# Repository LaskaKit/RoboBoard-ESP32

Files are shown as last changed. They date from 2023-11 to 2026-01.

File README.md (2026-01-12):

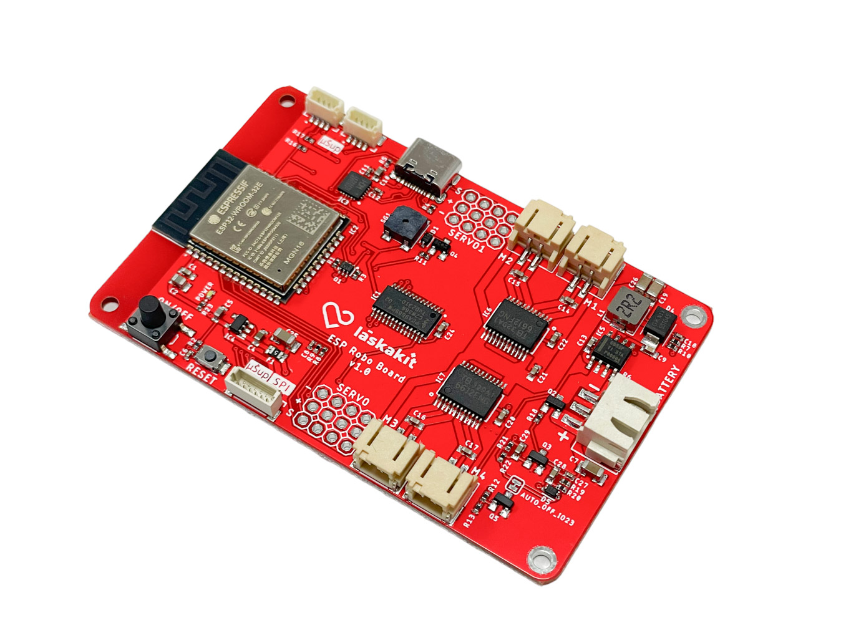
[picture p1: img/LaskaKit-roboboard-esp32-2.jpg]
RoboBoard-ESP32


# LaskaKit RoboBoard ESP32
Build a robot! Don't worry, it's nothing complicated. It's easy with our RoboBoard-ESP32. The RoboBoard has everything you need for a simple robot on it, and you can make it into a much more complex robot over time thanks to the expansion connectors for both the I2C and SPI bus. 

You can connect a lot of other peripherals. 

The basis of the whole board is ESP32 - it hides a great performance, the possibility to use Wi-Fi or Bluetooth interface and also a large community of DIY makers who have already invented many projects with it. It is not something unknown - ESP32 is one of the most well-known and used modules ever. 

The RoboBoard-ESP32 has a ready-to-use programmer (CH9102F), just plug the USB-C cable into the board and your computer, start the Arduino IDE and you can start programming. The converter-programmer will take care of uploading the program to the ESP32. 

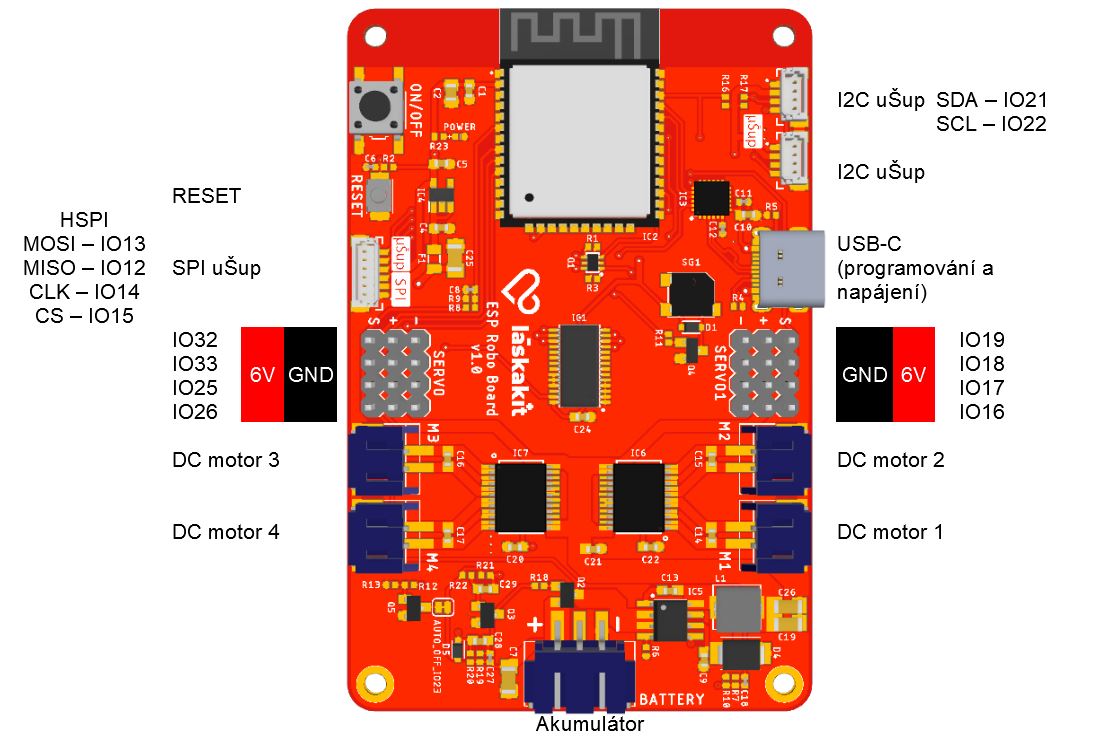
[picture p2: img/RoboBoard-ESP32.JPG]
RoboBoard-ESP32 pinout


The RoboBoard-ESP32 can drive up to 4 DC motors using PWM, thanks to the TB6612 driver. The maximum continuous current through one channel is 1A. The TB6612 DC motor driver is controlled via the PCA9685, which is controlled via the I2C bus. So you only need two wires (I2C, SDA - GPIO21 and SCL - GPIO22) to drive up to 4 DC motors. 

If you don't want to use DC motors or on the contrary you would like to add Servos to them, RoboBoard-ESP32 is ready for this option as well. 
You can connect up to 8 servo motors - what you use the servo motors for is up to you. The individual servo motors are controlled by GPIO16 to GPIO19, then GPIO25 and GPIO26 and lastly GPIO32 and GPIO33. 

What else have we prepared on the board? We have fitted a buzzer, you can control it via GPIO27. Then we have fitted two I2C ushup connectors to connect I2C sensors that are powered by 3.3V (SDA - GPIO21 and SCL - GPIO22) and one SPI ushup to connect other sensors or displays powered by 3.3V (CS - GPIO15, SDI/MOSI - GPIO13, CLK - GPIO14, SDO/MISO - GPIO12).

For the battery, we have a standard 3-pin JST-XH-3P connector where you plug in 2S LiPol batteries - for example this one https://www.laskakit.cz/rc-lipol-baterie-2s-1000mah-7-4v-20c-jst-bec/

The motors are powered via the LMR14050 step-down switching inverter from the 2S battery, which can deliver up to 5A. 

The battery voltage, via the voltage divider, is fed and measured by GPIO34. 

## New in version 2
- Powering via USB
- LiPol charging via USB
- uŠup IO port
- SK6812 RGB LED
- Overall more robust design

Sample codes will be prepared on our github at https://github.com/LaskaKit/RoboBoard-ESP32/tree/main/SW

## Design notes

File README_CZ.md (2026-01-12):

RoboBoard-ESP32

# LaskaKit RoboBoard ESP32 v2

Postav robota! Neboj, není to nic složitého. S naší deskou RoboBoard-ESP32 to bude hračka. RoboBoard totiž má na sobě všechno důležité pro jednoduchého robota a časem z něj můžeš udělat i mnohem komplexnějšího robota díky rozšiřujícím konektorům pro IO a navíc I2C a SPI sběrnice. 

Připojit tak můžeš bezpočet dalších periférií. 

Základem celé desky je ESP32 - ten v sobě skrývá velký výkon, možnost využít Wi-Fi nebo Bluetooth rozhraní a také velkou komunitu bastlířů, kteří s ním vymysleli už spoustu projektů. Nejdeš do neznámé vody - ESP32 je jeden z nejznámějších a nejpoužívanějších modulů vůbec. 

RoboBoard-ESP32 má na sobě už připravený programátor (CH9102F), stačí zapojit USB-C kabel do desky a tvého počítače, spustit Arduino IDE a můžeš začít programovat. Převodník-programátor se postará o nahrání programu do ESP32. 

RoboBoard-ESP32 pinout

RoboBoard-ESP32 může řídt až 4 DC motory pomocí PWM, díky driveru TB6612. Maximální trvalý proud skrze jeden kanál je 1A. Driver DC motorů TB6612 je řízen přes PCA9685, který je ovládán skrze I2C sběrnici. Takže ti stačí dva dráty (I2C, SDA - GPIO21 a SCL - GPIO22) k tomu, abys řídil až 4 DC motory. 

Pokud nechceš používat DC motory nebo naopak bys k nim chtěl přidat Serva, RoboBoard-ESP32 je připraven i na tuto možnost. 
Až 8 servo motorů můžeš připojit - k čemu servo motory použiješ už je jenom na tobě. Jednotlivé servo motory řídíš GPIO16 až GPIO19, dále pak GPIO25 a GPIO26 a poslední GPIO32 a GPIO33. 

Co dalšího jsme na desce ještě připravili? Osadili jsme bzučák, ten můžeš ovládat skrze GPIO27. Pak jsme osadili dva I2C uŠup konektor pro připojení I2C čidel, které jsou napájeny 3.3V (SDA - GPIO21 a SCL - GPIO22) a jeden SPI uŠup pro připojení dalších čidel či displejů napájených z 3.3V (CS - GPIO15, SDI/MOSI - GPIO13, CLK - GPIO14, SDO/MISO - GPIO12).

Pro baterii máme připraven standardní tří pinový konektor JST-XH-3P, kam zapojíš 2S LiPol baterie - například tuto https://www.laskakit.cz/rc-lipol-baterie-2s-1000mah-7-4v-20c-jst-bec/

Motory jsou napájené přes spínací step-down měnič LMR14050 z 2S baterie, který dokáže dodat až 5A. 

Napětí baterie, přes dělič napětí, je přivedeno a měřeno GPIO34. 

## Nově ve verzi 2
- Napájení přes USB
- Nabíjení LiPol baterie
- uŠup IO
- SK6812 RGB dioda
- Výrazně vyšší robustnost

Vzorové kódy budou připraveny na našem github na adrese https://github.com/LaskaKit/RoboBoard-ESP32/tree/main/SW

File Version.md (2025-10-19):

#### Version 2.0
- All new version.
- 2S Battery charger
#### Version 1.0
- Initial | Počáteční

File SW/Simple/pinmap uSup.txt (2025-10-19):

SPI uŠup
---------

MISO    12
MOSI    13
SCK     14
CS      15

I2C uŠup
--------

SDA     21
SCL     22

IO uŠup
--------

IO      5

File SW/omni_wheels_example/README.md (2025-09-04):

# Laska Omni Car Example

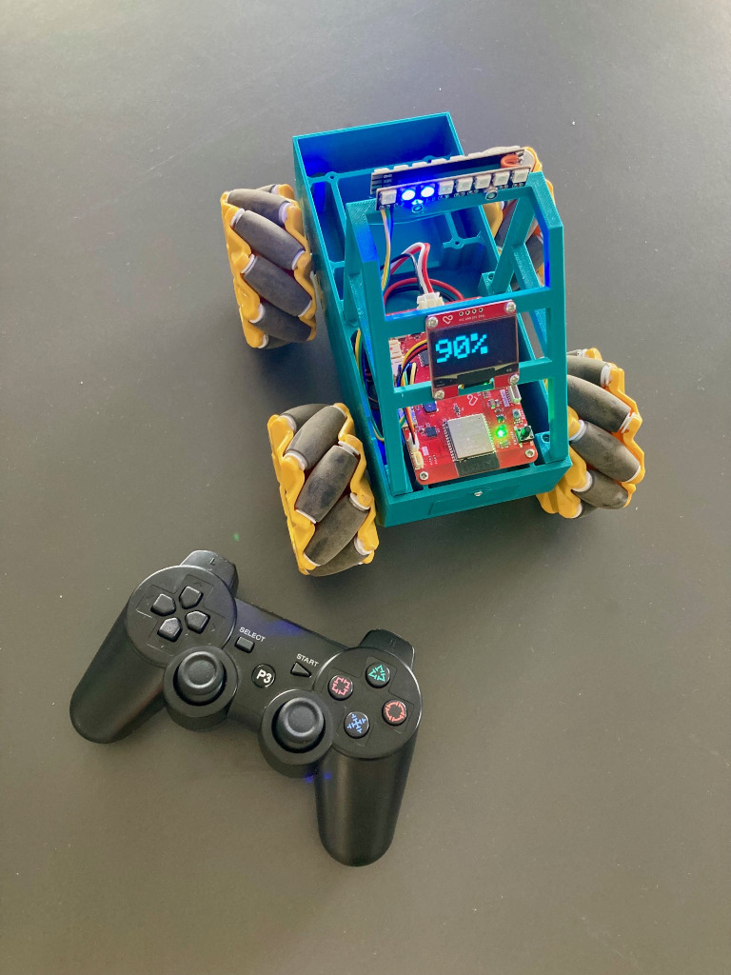
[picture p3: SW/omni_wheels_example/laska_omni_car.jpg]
Laska OmniCar


This example consists of 2 parts.

1. The vehicle with omni wheels.
2. The gamepad for vehicle control.

The vehicle and gamepad are communicating via ESP-NOW protocol.

## How to setup

1. Optain MAC addresses of gamepad and the roboboard using the sketch in `get_mac_address` directory.
2. Set the MAC address of the gamepad in the `fw_laska_omni_car` sketch and flash the roboboard.
3. Set the MAC address of the roboboard in the `fw_laska_omni_gamepad` sketch and flash the gamepad.
4. Enjoy!

### Optionally

You can setup your own LMK and PMK keys to keep the communication between roboboard and gamepad secure.
Note that keys on roboboard must be identical to those on gamepad.

## Controls

| *Input* | *Description* |
| --- | --- |
| left stick (left/right) | left/right spin |
| right stick (up/down) | forward/backward motion |
| right stick (left/right) | left/right motion |
| L1 | headlights |
| triangle | starts the beacon |
| square | stops the beacon |
| cross | horn |
| P3 (1.5s hold) | power off |

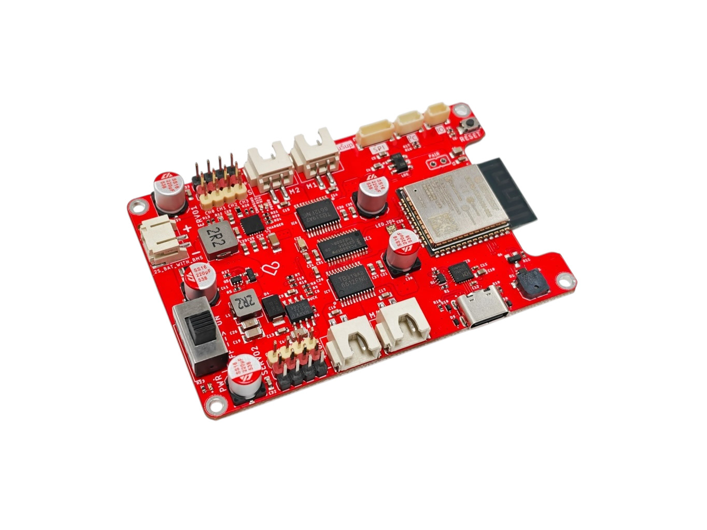
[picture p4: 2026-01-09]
img/LaskaKit-roboboard-esp32-v2-3.jpg

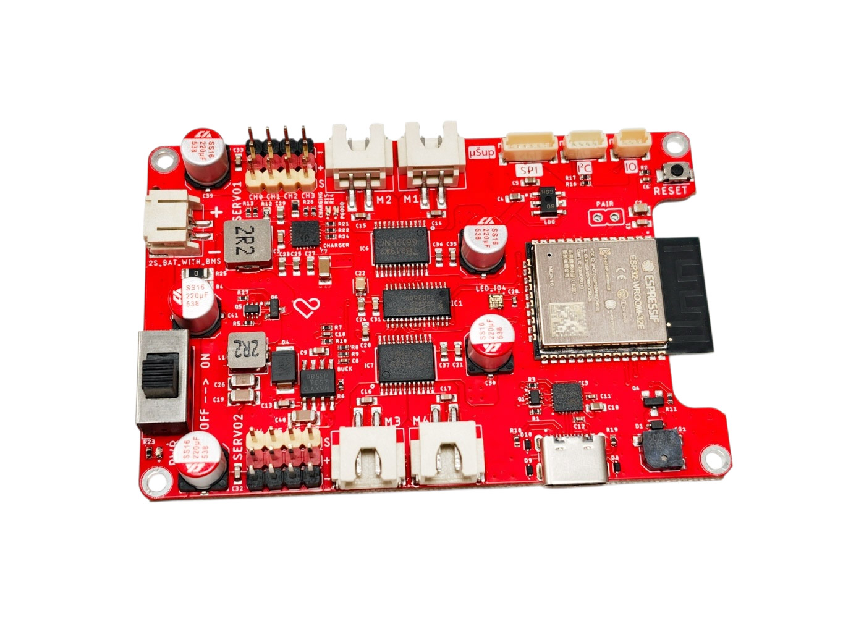
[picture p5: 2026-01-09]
img/LaskaKit-roboboard-esp32-v2-2.jpg

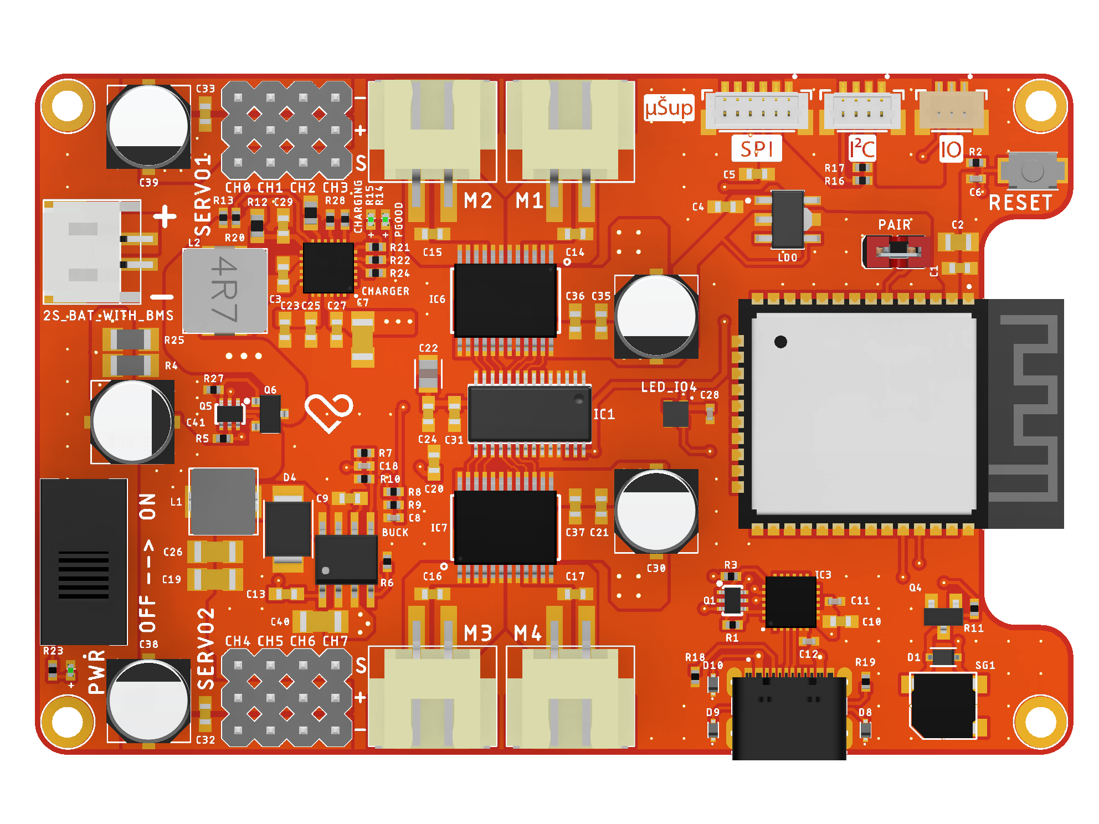
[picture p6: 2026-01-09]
img/roboboard-esp32-v2_top_render.png

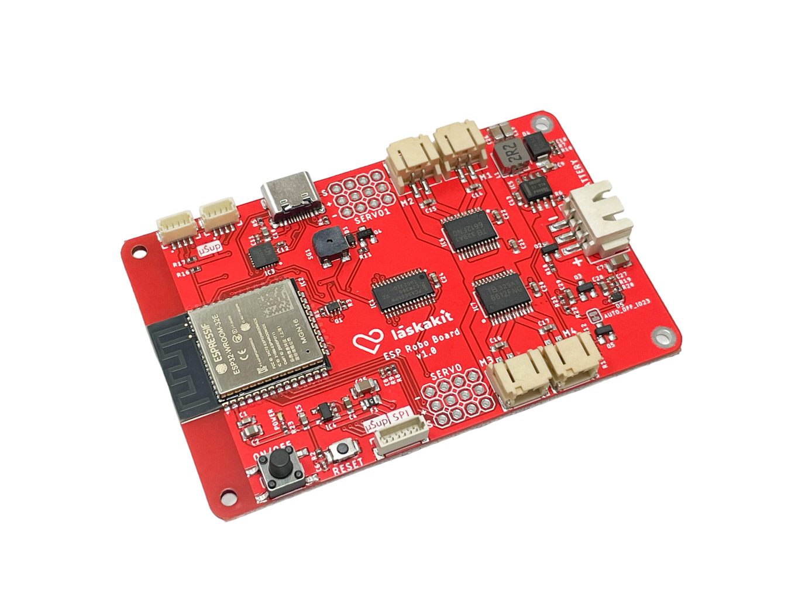
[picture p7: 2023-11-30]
img/V1/LaskaKit-roboboard-esp32-1.jpg

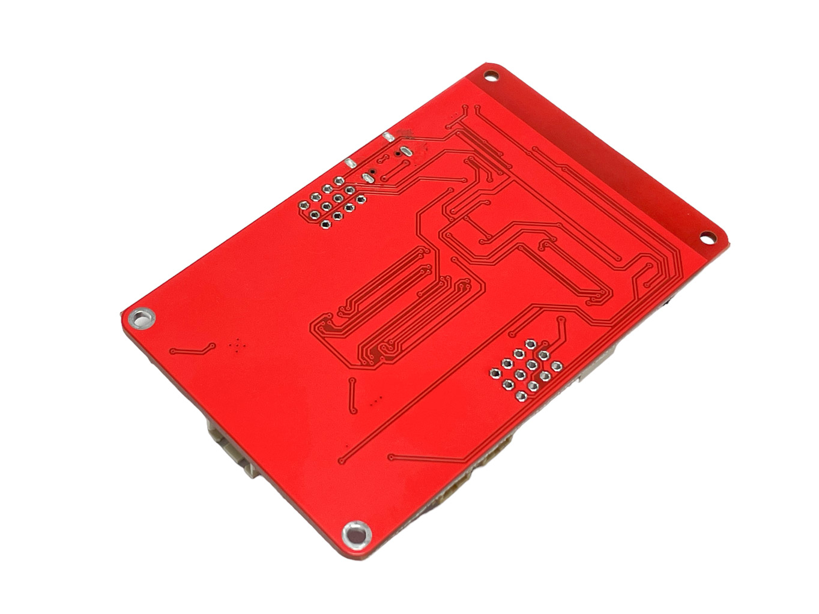
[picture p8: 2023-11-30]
img/V1/LaskaKit-roboboard-esp32-3.jpg

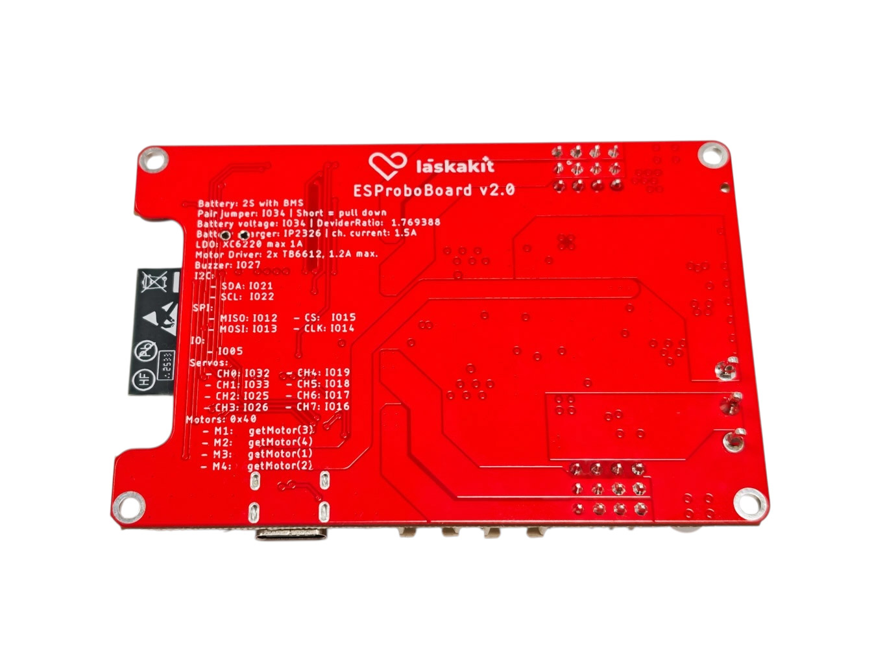
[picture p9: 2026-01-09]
img/LaskaKit-roboboard-esp32-v2-5.jpg

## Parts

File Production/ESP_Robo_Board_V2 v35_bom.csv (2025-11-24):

Comment | Designator | Footprint | LCSC Part #
0.5R | R12 | R0603
0R | R4 R25 | R1206
1N4148 | D1 | SOD323-R | C94001
1k | R11 R14 R15 R21 R22 | R0402
2.2uH | L1 | L5.4X5.2 | C351096
2.2uH | L2 | L6.6X7 | C167218
2S bat with BMS | 2S_BAT_WITH_BMS | S2B-PH-SM4 | C47647
3.3k | R23 | R0402
4.7k | R16 R17 | R0402
4.7uF | C24 | C0603
5.1k | R13 R18 R19 | R0402
8.2nF | C9 | C0603
10k | R1 R2 R3 | R0402
10uF | C23 C25 C27 C29 C36 C37 | C0603
10uF/10V | C5 | C0603 | C19666
10uF/16 | C4 | C0603
13k | R10 | R0402
20k | R6 | R0402
22uF | C10 | C0603
47k | R5 R27 | R0402
47uF | C2 | C0805
51k | R20 R24 | R0402
59.7k | R28 | R0603
91k | R7 | R0402
100k | R8 | R0402
100nF | C1 C3 | C0603
100nF | C6 C8 C11 C12 | C0402
100nF | C13 C14 C15 C16 C17 C20 C21 | C0603
100nF | C28 | C0402
100nF | C31 C32 C33 C35 | C0603
100uF | C7 C19 | C1206
100uF | C22 | C0805 | C141660
100uF | C26 C40 | C1206
130k | R9 | R0402
220uF/16V 5-20m? | C30 C34 C38 C39 C41 | UD-6 3X7 7_NICHICON | C3035876
330pF | C18 | C0402
CH9102F | IC3 | QFN24-4X4
DMG2305UX | Q6 | MICRO3 | C144153
ESP32-WROOM-32E | IC2 | ESP32WROOM32E | C701343
FUET-5020 | SG1 | FUET-5020 | C391029
GREEN | DONE POWER | CHIPLED_0402 | C130722
IP2326 | CHARGER | QFN24-4X4 | C5441281
JST-SH-3P | J4 | 1X03_1MM_RA_VERT | C160389
JST-SH-4P | J3 | 1X04_1MM_RA_VERT | C371588
JST-SH-6P | J1 | 1X06_1MM_RA_VERT | C145963
JST-XH-2/90SMD | M1 M2 M3 M4 | S2B-XH-SM4
LESD5D5.0CT1G | D8 D9 D10 | LESD5D50CT1G
LMR14050DDAR | BUCK | SO08-EPAD | C155484
MMDT3904 | Q1 | SC70-6 | C268586
MMDT5401 | Q5 | SC70-6 | C54540
PCA9685PW 118 | IC1 | TSSOP28 | C2678753
RED | CHARGING | CHIPLED_0402
S9013 | Q4 | SOT23-BEC | C52801
SK6812-EC20 | LED_IO4 | SK6812EC20
SS1045-SMB | D4 | SMB | C2903947
TB6612FNG | IC6 IC7 | SSOP24
TS-1088R-02026 | RESET | TS1088R02026 | C455280
USB-C_GT-USB-7010B | J2 | G-SWITCH_GT-USB-7010B | C2837092
XC6220B331PR-G | LDO | XC6220B331PRG
SS-12D10L5 | S1 | SS-12D10L5 | C319012
PINHD_1X4_BLACK | 2 6 | PINHD_1X4_BLACK | C2691448
PINHD_1X4_RED | 1 5 | PINHD_1X4_RED | C41425294
PINHD_1X4_YELLOW | SERVO1 SERVO2 | PINHD_1X4_YELLOW | C41425307

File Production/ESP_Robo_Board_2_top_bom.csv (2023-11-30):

Comment | Designator | Footprint | LCSC Part #
1M | R8 | R0402
1N4148 | D1 D5 | SOD323-R
1k | R11 R23 | R0402
1uF | C28 C29 | C0603
2.2uH | L1 | L5.4X5.2 | C351096
4.7k | R16 R17 | R0402
5.1k | R4 R5 | R0402
8.2n | C9 | C0603
10k | R1 R2 R3 R12 R20 | R0402
13k | R10 | R0402
20k | R6 | R0402
22uF | C4 C5 C10 | C0603
47uF | C2 | C0805
91k | R7 | R0402
100k | R13 R18 R19 R21 | R0402
100n | C11 C12 | C0402
100n | C13 C14 C15 C16 C17 C20 C21 C22 C24 | C0603
100nF | C1 | C0603
100nF | C6 C8 C27 | C0402
100uF | C7 C19 C25 C26 | C1206
330p | C18 | C0402
620k | R9 R22 | R0402
0805L050 | F1 | 0805L | C66452
AO3400 | Q3 Q5 | SOT23 | C693097
CH9102F | IC3 | QFN24-4X4
ESP32-WROOM-32E | IC2 | ESP32WROOM32E
FUET-5020 | SG1 | FUET-5020 | C391029
GREEN | POWER | CHIPLED_0402
JST-PH-2/90SMD | M1 M2 M3 M4 | S2B-PH-SM4 | C47647
JST-SH-4P | J3 J5 | 1X04_1MM_RA_VERT | C371588
JST-SH-6P | J1 | 1X06_1MM_RA_VERT | C145963
JST-XH-3P/90SMD | BATTERY | S3B-XH-SM4
LMR14050DDAR | IC5 | SO08-EPAD | C155484
ME6211C33M5G | IC4 | SOT23-5
MMDT3904 | Q1 | SC70-6 | C268586
PCA9685PW 118 | IC1 | TSSOP28 | C2678753
PJM07P20SA | Q2 | SOT23 | C2856842
S9013 | Q4 | SOT23-BEC | C52801
SS1045-SMB | D4 | SMB | C2903947
TB6612FNG | IC6 IC7 | SSOP24
TS-1088R-02026 | RESET | TS1088R02026 | C455280
TS-1102S-B-H-B | ON/OFF | B3F-SMD
USB-C_2-16PIN | J4 | USBC_USB-C-16P-5 | C2837092

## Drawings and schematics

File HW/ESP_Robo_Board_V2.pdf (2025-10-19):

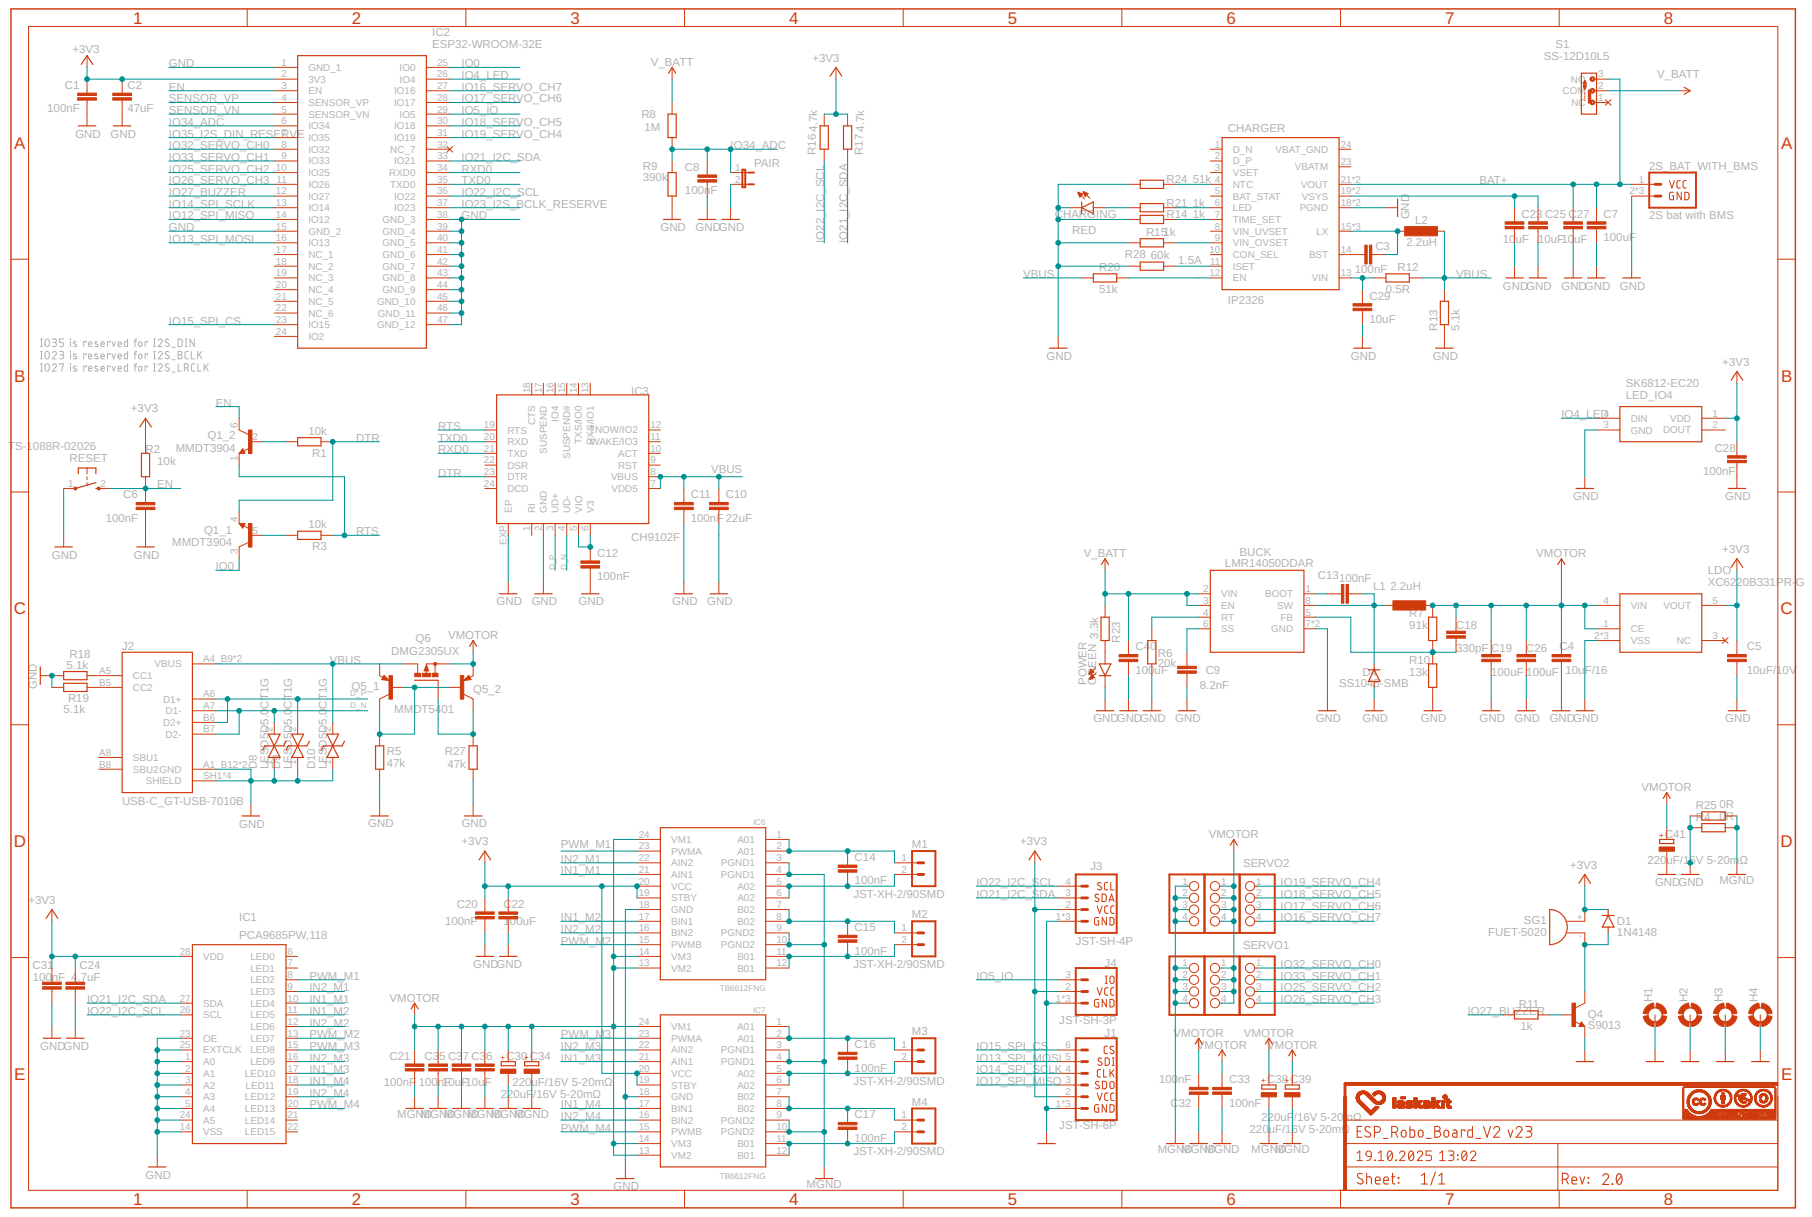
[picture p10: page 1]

IC2 GND_1

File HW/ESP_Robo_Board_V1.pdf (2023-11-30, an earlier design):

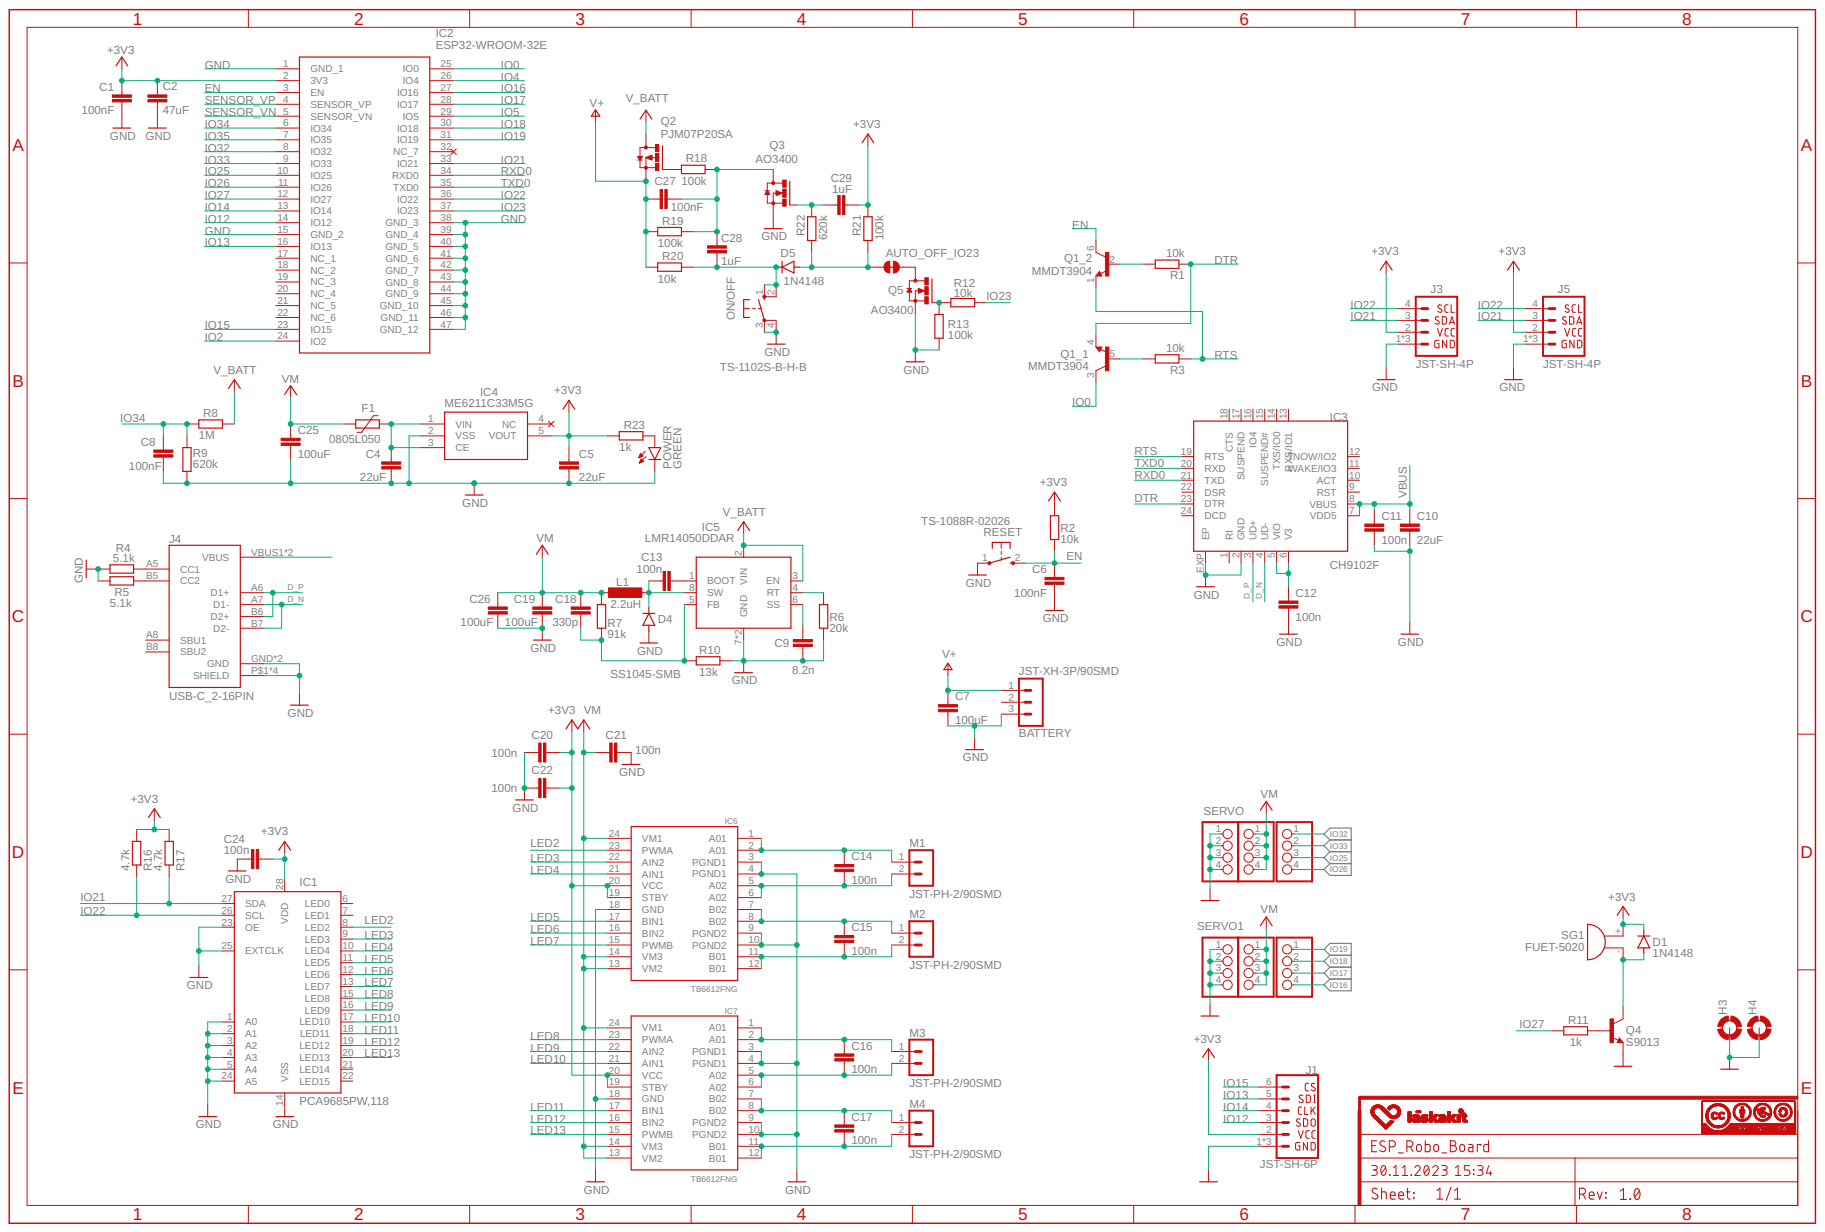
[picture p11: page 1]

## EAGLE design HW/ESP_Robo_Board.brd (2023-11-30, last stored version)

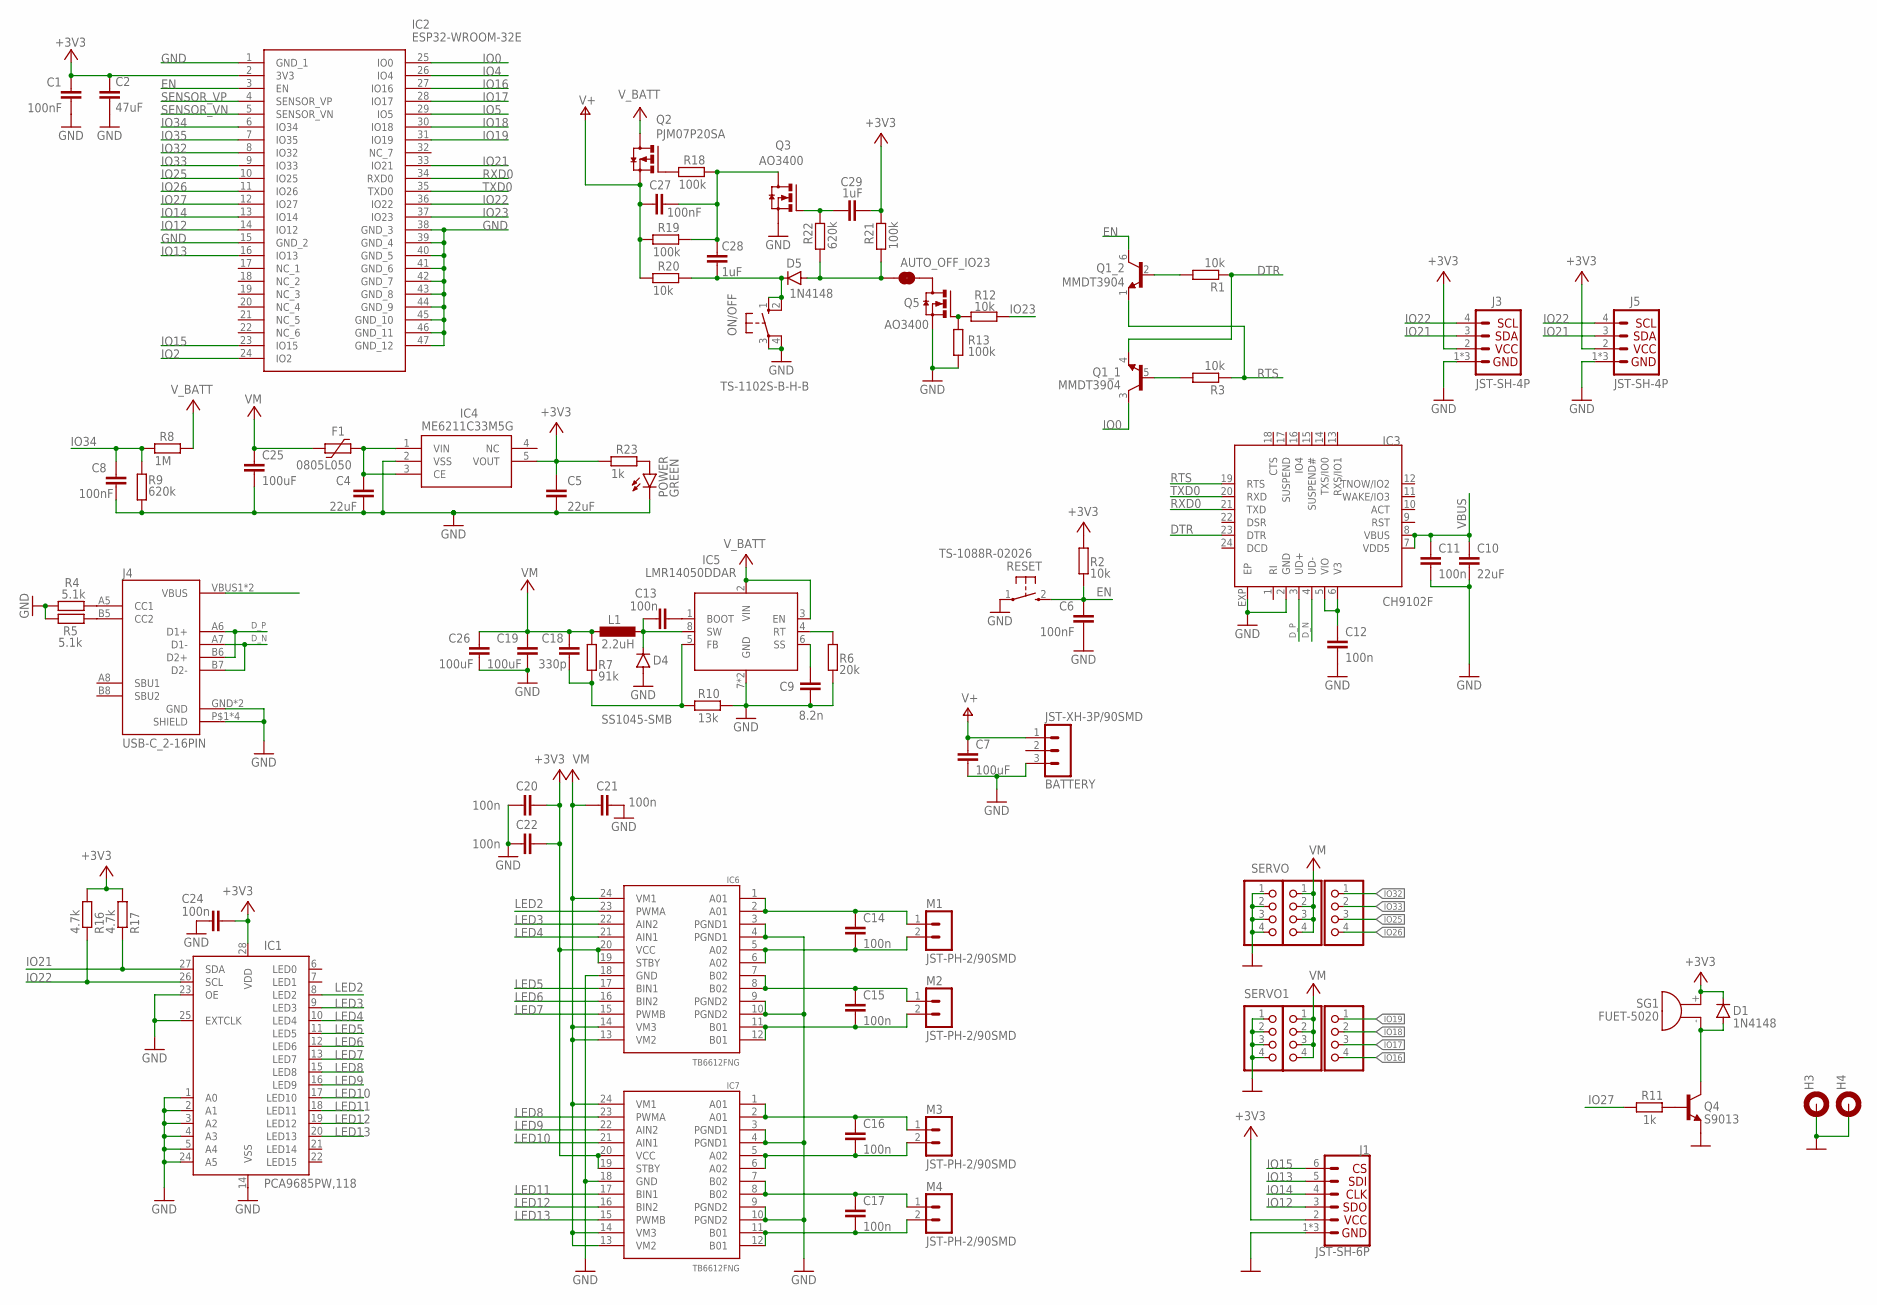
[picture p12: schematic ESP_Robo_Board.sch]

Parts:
1, 5: PINHD_1X4_RED; 1X04
2, 6: PINHD_1X4_BLACK; 1X04
AUTO_OFF_IO23: nv; SMT-JUMPER_2_NC_TRACE_SILK
BATTERY: JST-XH-3P/90SMD; S3B-XH-SM4
C1: 100nF; C0603
C2: 47uF; C0805
C4, C10: 22uF; C0603
C5: 22uF; C0603; LCSC_PART C19666
C6, C8, C27: 100nF; C0402
C7, C19, C25, C26: 100uF; C1206
C9: 8.2n; C0603
C11, C12: 100n; C0402
C13, C14, C15, C16, C17, C20, C21, C22, C24: 100n; C0603
C18: 330p; C0402
C28, C29: 1uF; C0603
D1: 1N4148; SOD323-R; LCSC_PART C94001
D4: SS1045-SMB; SMB; LCSC_PART C2903947
D5: 1N4148; SOD323-R
F1: 0805L050; 0805L; LCSC_PART C66452
H3, H4: MOUNT-PAD-ROUND2.5; 2,5-PAD
IC1: PCA9685PW,118; TSSOP28
IC2: ESP32-WROOM-32E; ESP32WROOM32E
IC3: CH9102F; QFN24-4X4
IC4: ME6211C33M5G; SOT23-5
IC5: LMR14050DDAR; SO08-EPAD
IC6, IC7: TB6612FNG; SSOP24
J1: JST-SH-6P; 1X06_1MM_RA_VERT
J3, J5: JST-SH-4P; 1X04_1MM_RA_VERT
J4: USB-C_2-16PIN; USBC_USB-C-16P-5
L1: 2.2uH; L5.4X5.2; LCSC_PART C351096
M1, M2, M3, M4: JST-PH-2/90SMD; S2B-PH-SM4
ON/OFF: TS-1102S-B-H-B; B3F-SMD
POWER: GREEN; CHIPLED_0402
Q1: MMDT3904; SC70-6; LCSC_PART C268586
Q2: PJM07P20SA; SOT23; LCSC_PART C2856842
Q3, Q5: AO3400; SOT23; LCSC_PART C693097
Q4: S9013; SOT23-BEC; LCSC_PART C52801
R1, R2, R3, R12, R20: 10k; R0402
R4, R5: 5.1k; R0402
R6: 20k; R0402
R7: 91k; R0402
R8: 1M; R0402
R9, R22: 620k; R0402
R10: 13k; R0402
R11: 1k; R0402; LCSC_PART C22548
R13, R18, R19, R21: 100k; R0402
R16, R17: 4.7k; R0402
R23: 1k; R0402
RESET: TS-1088R-02026; TS1088R02026; LCSC_PART C455280
SERVO, SERVO1: PINHD_1X4_YELLOW; 1X04
SG1: FUET-5020

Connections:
+3V3: C1.1, C2.1, C5.1, C20.2, C22.2, C24.2, C29.1, D1.C, IC1.28 (VDD), IC2.2 (3V3), IC4.5 (VOUT), IC6.19 (STBY), IC6.20 (VCC), IC7.19 (STBY), IC7.20 (VCC), J1.2 (VCC), J3.2 (VCC), J5.2 (VCC), R2.1, R16.2, R17.2, R21.2, R23.1, SG1.+
+6V: 1.1, 1.2, 1.3, 1.4, 5.1, 5.2, 5.3, 5.4, C18.1, C19.1, C21.1, C25.1, C26.1, F1.2, IC6.13 (VM2), IC6.14 (VM3), IC6.24 (VM1), IC7.13 (VM2), IC7.14 (VM3), IC7.24 (VM1), L1.2, R7.1
DTR: IC3.23 (DTR), Q1.4 (E), R1.1
D_N: IC3.4 (UD-), J4.A7 (D1-), J4.B7 (D2-)
D_P: IC3.3 (UD+), J4.A6 (D1+), J4.B6 (D2+)
EN: C6.1, IC2.3 (EN), Q1.6 (C), R2.2, RESET.2 (3)
GND: 2.1, 2.2, 2.3, 2.4, 6.1, 6.2, 6.3, 6.4, BATTERY.3 (1), C1.2, C2.2, C4.2, C5.2, C6.2, C7.2, C8.2, C9.2, C10.2, C11.2, C12.2, C19.2, C20.1, C21.2, C22.1, C24.1, C25.2, C26.2, D4.A, H3.1, H4.1, IC1.1 (A0), IC1.2 (A1), IC1.3 (A2), IC1.4 (A3), IC1.5 (A4), IC1.14 (VSS), IC1.23 (OE), IC1.24 (A5), IC1.25 (EXTCLK), IC2.1 (GND_1), IC2.15 (GND_2), IC2.38 (GND_3), IC2.39 (GND_4), IC2.40 (GND_5), IC2.41 (GND_6), IC2.42 (GND_7), IC2.43 (GND_8), IC2.44 (GND_9), IC2.45 (GND_10), IC2.46 (GND_11), IC2.47 (GND_12), IC3.2 (GND), IC3.EXP (EP), IC4.2 (VSS), IC5.7 (GND), IC5.EPAD (GND), IC6.3 (PGND1), IC6.4 (PGND1), IC6.9 (PGND2), IC6.10 (PGND2), IC6.18 (GND), IC7.3 (PGND1), IC7.4 (PGND1), IC7.9 (PGND2), IC7.10 (PGND2), IC7.18 (GND), J1.1 (GND), J1.NC1 (GND), J1.NC2 (GND), J3.1 (GND), J3.NC1 (GND), J3.NC2 (GND), J4.GND, J4.GND2 (GND), J4.P$1 (SHIELD), J4.P$2 (SHIELD), J4.P$3 (SHIELD), J4.P$4 (SHIELD), J5.1 (GND), J5.NC1 (GND), J5.NC2 (GND), ON/OFF.3, ON/OFF.4 (P1), POWER.C, Q3.2 (S), Q4.E, Q5.2 (S), R4.1, R5.1, R6.2, R9.1, R10.2, R13.1, RESET.1
IO0: IC2.25 (IO0), Q1.3 (C)
IO2: IC2.24 (IO2)
IO4: IC2.26 (IO4)
IO5: IC2.29 (IO5)
IO12: IC2.14 (IO12), J1.3 (SDO)
IO13: IC2.16 (IO13), J1.5 (SDI)
IO14: IC2.13 (IO14), J1.4 (CLK)
IO15: IC2.23 (IO15), J1.6 (CS)
IO16: IC2.27 (IO16), SERVO1.4
IO17: IC2.28 (IO17), SERVO1.3
IO18: IC2.30 (IO18), SERVO1.2
IO19: IC2.31 (IO19), SERVO1.1
IO21: IC1.27 (SDA), IC2.33 (IO21), J3.3 (SDA), J5.3 (SDA), R17.1
IO22: IC1.26 (SCL), IC2.36 (IO22), J3.4 (SCL), J5.4 (SCL), R16.1
IO23: IC2.37 (IO23), R12.2
IO25: IC2.10 (IO25), SERVO.3
IO26: IC2.11 (IO26), SERVO.4
IO27: IC2.12 (IO27), R11.1
IO32: IC2.8 (IO32), SERVO.1
IO33: IC2.9 (IO33), SERVO.2
IO34: C8.1, IC2.6 (IO34), R8.1, R9.2
IO35: IC2.7 (IO35)
LED2: IC1.8 (LED2), IC6.23 (PWMA)
LED3: IC1.9 (LED3), IC6.22 (AIN2)
LED4: IC1.10 (LED4), IC6.21 (AIN1)
LED5: IC1.11 (LED5), IC6.17 (BIN1)
LED6: IC1.12 (LED6), IC6.16 (BIN2)
LED7: IC1.13 (LED7), IC6.15 (PWMB)
LED8: IC1.15 (LED8), IC7.23 (PWMA)
LED9: IC1.16 (LED9), IC7.22 (AIN2)
LED10: IC1.17 (LED10), IC7.21 (AIN1)
LED11: IC1.18 (LED11), IC7.17 (BIN1)
LED12: IC1.19 (LED12), IC7.16 (BIN2)
LED13: IC1.20 (LED13), IC7.15 (PWMB)
unnamed: C4.1, F1.1, IC4.1 (VIN), IC4.3 (CE)
unnamed: J4.A5 (CC1), R4.2
unnamed: C13.1, D4.C, IC5.8 (SW), L1.1
unnamed: Q1.5 (B), R3.2
unnamed: C9.1, IC5.6 (SS)
unnamed: IC5.4 (RT), R6.1
unnamed: J4.B5 (CC2), R5.2
unnamed: Q4.B, R11.2
unnamed: POWER.A, R23.2
unnamed: C13.2, IC5.1 (BOOT)
unnamed: Q1.2 (B), R1.2
unnamed: Q5.1 (G), R12.1, R13.2
unnamed: D1.A, Q4.C, SG1.-
unnamed: C12.1, IC3.5 (VIO), IC3.6 (V3)
unnamed: AUTO_OFF_IO23.2, Q5.3 (D)
unnamed: C18.2, IC5.5 (FB), R7.2, R10.1
unnamed: C14.1, IC6.1 (A01), IC6.2 (A01), M1.1
unnamed: C14.2, IC6.5 (A02), IC6.6 (A02), M1.2
unnamed: C15.1, IC6.7 (B02), IC6.8 (B02), M2.1
unnamed: Q2.1 (G), R18.1
unnamed: C15.2, IC6.11 (B01), IC6.12 (B01), M2.2
unnamed: C16.1, IC7.1 (A01), IC7.2 (A01), M3.1
unnamed: C28.2, D5.C, ON/OFF.1 (S), ON/OFF.2 (S1), R20.2
unnamed: C16.2, IC7.5 (A02), IC7.6 (A02), M3.2
unnamed: C17.1, IC7.7 (B02), IC7.8 (B02), M4.1
unnamed: C27.2, C28.1, Q3.3 (D), R18.2, R19.2
unnamed: C17.2, IC7.11 (B01), IC7.12 (B01), M4.2
unnamed: C29.2, Q3.1 (G), R22.2
unnamed: AUTO_OFF_IO23.1, D5.A, R21.1, R22.1
RTS: IC3.19 (RTS), Q1.1 (E), R3.1
RXD0: IC2.34 (RXD0), IC3.21 (TXD)
SENSOR_VN: IC2.5 (SENSOR_VN)
SENSOR_VP: IC2.4 (SENSOR_VP)
TXD0: IC2.35 (TXD0), IC3.20 (RXD)
V+: BATTERY.1 (3), C7.1, C27.1, Q2.2 (S), R19.1, R20.1
VBUS: C10.1, C11.1, IC3.7 (VDD5), IC3.8 (VBUS), J4.VBUS1 (VBUS), J4.VBUS2 (VBUS)
V_BATT: IC5.2 (VIN), IC5.3 (EN), Q2.3 (D), R8.2

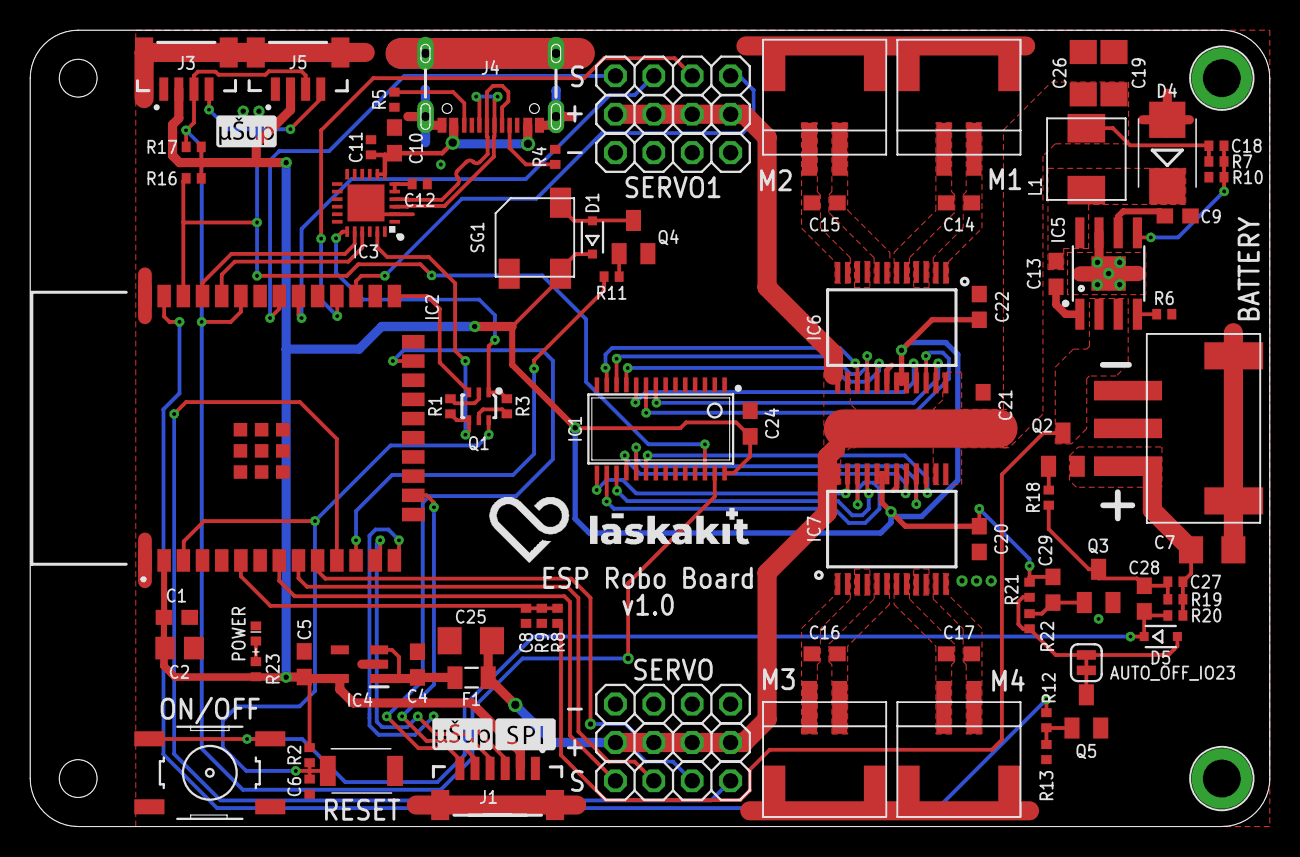
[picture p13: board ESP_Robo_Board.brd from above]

Board: 2 copper layers, 82.0 x 52.7 mm, 91 parts (0 on the bottom side), 72 nets.

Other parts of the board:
U$1, U$2: USUP_4MM_SILKSCREEN
U$3: LASKKIT_20MM_SILKSCREEN
U$4: SPI_4MM_SILKSCREEN

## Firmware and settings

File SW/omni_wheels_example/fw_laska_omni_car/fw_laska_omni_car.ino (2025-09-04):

/*
  Example code for LaskaKit RoboBoard ESP32. This example contains
  the FW for the 'car' with omni wheels that is controlled from gamepad
  using esp-now protocol.

  Arduino IDE setting
    Board: ESP32 Dev Module

  Board:   LaskaKit RoboBoard ESP32
           https://www.laskakit.cz/laskakit-roboboard-esp32/?variantId=13424
  Motors:  TT motor - steel gears
           https://www.laskakit.cz/tt-motor-s-prevodovkou-plastove-prevody/ 
  Wheels:  Mecanum Omni Wheels
           https://www.laskakit.cz/sada-4ks-mecanum-omni-kol-60mm/
  Display: LaskaKit OLED display 128x64 1.3"
           https://www.laskakit.cz/laskakit-oled-displej-128x64-1-3--i2c/
  LEDs:    8x intelligent RGB LED NeoPixel strip
           https://www.laskakit.cz/8x-inteligentni-rgb-led-neopixel-pasek--ws2812b--5050--5v/

  Email:   podpora@laskakit.cz
  Web:     laskakit.cz
*/

#include <Adafruit_GFX.h>
#include <Adafruit_MotorShield.h>
#include <Adafruit_SH110X.h>
#include <ESP32AnalogRead.h>
#include <WiFi.h>
#include <esp_now.h>

#include "laskacar.hpp"
#include "laskacar_beacon.hpp"
#include "laskagamepad.hpp"


// CONFIG ////////////////////////////////////////////////////////////////////////

// here specify the mac address of your gamepad
// the mac address can be optained from running
// the get_mac_address sketch
const uint8_t gamepad_mac_address[6] = {0x80, 0x65, 0x99, 0x96, 0x6B, 0x3C};

// type your super secret keys here (16 bytes each)
const char *PMK_KEY_STR = "laskakit_pmk_key";
const char *LMK_KEY_STR = "laskakit_lmk_key";

// ENDCONFIG ////////////////////////////////////////////////////////////////////


#define DIVIDER_RATIO 2.599
// 8.4V 100%
// 6.0V   0%

#define ADCpin 34
ESP32AnalogRead adc;

#define PIN_BUZZ 27
#define low_batt 6.7
#define AUTO_OFF 23

// disable Adafruit splash logo
#define SH110X_NO_SPLASH

Adafruit_MotorShield AFMS = Adafruit_MotorShield(0x40);
Adafruit_DCMotor *BackLeftMotor = AFMS.getMotor(4);
Adafruit_DCMotor *BackRightMotor = AFMS.getMotor(1);
Adafruit_DCMotor *FrontRightMotor = AFMS.getMotor(3);
Adafruit_DCMotor *FrontLeftMotor = AFMS.getMotor(2);
LaskaOmniCar laska_omni_car(BackLeftMotor, BackRightMotor, FrontLeftMotor,
                            FrontRightMotor);

struct Message {
  LaskaGamepad gamepad_inputs;
  uint8_t battery_v; // voltage * 10
};
Message m;

float battery_car_v;
unsigned long previousMillis = 0;

Beacon beacon(16);
LeftRightBeaconPattern lrbp(&beacon);

Adafruit_SH1106G display(128, 64, &Wire);

int display_refresh = 0;
unsigned long gamepad_watchdog_timer = 0;

esp_now_peer_info_t peerInfo;

// esp-now callback
void OnDataRecv(const uint8_t *mac_addr, const uint8_t *data, int data_len) {
  // char macStr[18];
  // snprintf(macStr, sizeof(macStr), "%02x:%02x:%02x:%02x:%02x:%02x",
  //          mac_addr[0], mac_addr[1], mac_addr[2], mac_addr[3], mac_addr[4],
  //          mac_addr[5]);

  // Serial.println(macStr);
  // Serial.println(data_len);

  if (data_len != sizeof(m)) {
    return;
  }

  memcpy(&m, data, sizeof(m));
  laska_omni_car.move(m.gamepad_inputs.right_stick_y >> 7,
                      m.gamepad_inputs.right_stick_x >> 7,
                      m.gamepad_inputs.left_stick_x >> 7);
  gamepad_watchdog_timer = millis();
}

uint8_t get_battery_status() {
  float empty = 6.0, full = 8.4;
  battery_car_v = adc.readVoltage() * DIVIDER_RATIO;
  uint8_t battery_car_percent = 100 * (battery_car_v - empty) / (full - empty);
  return battery_car_percent;
}

void display_battery_status() {
  display.clearDisplay();
  display.setCursor(0, 10);
  display.print(get_battery_status());
  display.print("%");
}

void poweroff(void) {
  tone(PIN_BUZZ, 500, 500);
  digitalWrite(AUTO_OFF, HIGH);
}

void setup() {
  Serial.begin(115200);
  delay(500);

  pinMode(AUTO_OFF, OUTPUT);
  digitalWrite(AUTO_OFF, LOW);

  // display
  display.begin(0x3C, true); // Address 0x3C default
  display.setTextColor(SH110X_WHITE);
  display.setTextSize(5);

  // battery voltage measurement
  adc.attach(ADCpin);
  display_battery_status();

  // start adafruit motor shield
  AFMS.begin();

  WiFi.mode(WIFI_STA);

  if (esp_now_init() != ESP_OK) {
    Serial.println("esp now failed");
  } else {
    Serial.println("esp now OK");
  }
  esp_now_set_pmk((uint8_t *)PMK_KEY_STR);

  // Once ESPNow is successfully Init, we will register for recv CB to
  // get recv packer info.
  esp_now_register_recv_cb(OnDataRecv);

  // setup peer info
  memcpy(peerInfo.peer_addr, gamepad_mac_address, 6);
  peerInfo.channel = 0;
  peerInfo.encrypt = true;
  memcpy(peerInfo.lmk, LMK_KEY_STR, 16);
  if (esp_now_add_peer(&peerInfo) != ESP_OK) {
    Serial.println("Failed to add peer");
  }

  // signal that setup is complete
  tone(PIN_BUZZ, 1000, 200);
}

int powering_off_start = 0;
bool powering_off = false;

void loop() {
  // gamepad connection watchdog
  unsigned long current = millis();
  if (current - gamepad_watchdog_timer >= 200) {
    laska_omni_car.move(0, 0, 0); // stop the car
    m.gamepad_inputs.buttons = 0; // unpress all buttons
  }

  // handle power off from gamepad
  // hold the P3 buttot for 1.5s to poweroff
  if (m.gamepad_inputs.off && !powering_off) {
    powering_off_start = millis();
    powering_off = true;
  } else if (m.gamepad_inputs.off && millis() - powering_off_start >= 1500) {
    poweroff();
  } else if (!m.gamepad_inputs.off) {
    powering_off = false;
  }

  display_refresh++;
  // refresh once every 10s
  if (display_refresh > 20 * 10) {
    display_battery_status();
    display.display();
    display_refresh = 0;
  }

  // make noise when cross is pressed
  if (m.gamepad_inputs.get_button(LaskaGamepadButton::CROSS)) {
    tone(PIN_BUZZ, 500, 55);
  }

  // start beacon when triangle is pressed
  if (m.gamepad_inputs.get_button(LaskaGamepadButton::TRIANGLE)) {
    lrbp.init();
  }

  // stop beacon when square is pressed
  if (m.gamepad_inputs.get_button(LaskaGamepadButton::SQUARE)) {
    beacon.leds_state = 0;
  }

  // handle the beacon lighting
  lrbp.step();
  beacon.write();

  // full light front when l1 is pressed
  // must be handled after beacon lighting to override it
  if (m.gamepad_inputs.get_button(LaskaGamepadButton::L1)) {
    beacon.leds.fill(beacon.leds.Color(255, 255, 255), 8, 8);
  }

  beacon.leds.show();
  delay(50);
}

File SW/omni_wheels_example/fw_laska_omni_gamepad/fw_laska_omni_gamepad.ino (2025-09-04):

/*
  Example code for the LaskaKit gamepad based on ESP32C3
  which controls the `car` with omni wheels based od LaskaKit RoboBoard ESP32.

  Arduino IDE setting
    Board: ESP32C3 Dev Module

  Email: podpora@laskakit.cz
  Web:   laskakit.cz
*/

#include "ADS1X15.h" //Rob Tillaart ADS1X15 Library
#include "PCF8575.h" //Rob Tillaart PCF8575 Library
#include <Adafruit_NeoPixel.h>
#include <ESP32AnalogRead.h>
#include <WiFi.h>
#include <Wire.h>
#include <esp_now.h>

#include "laskagamepad.hpp"


// CONFIG ///////////////////////////////////////////////////////////////////////////////////

// here specify the mac address of your robo board (car)
// the mac address can be optained from running
// the get_mac_address.ino sketch
const uint8_t car_mac_address[6] = {0x08, 0xD1, 0xF9, 0xC4, 0x60, 0xE4};

// type your super secret keys here (16 bytes each)
// keys on car and gamepad must be the same
const char *PMK_KEY_STR = "laskakit_pmk_key";
const char *LMK_KEY_STR = "laskakit_lmk_key";

// END OF CONFIG ///////////////////////////////////////////////////////////////////////////////////


// adc sticks, L2, R2
ADS1115 ADS(0x49);

// buttons, io expander
PCF8575 PCF(0x20);

// neopixel led
#define BRIGHTNESS 10
#define LED_PIN 4
#define NUM_LED 3
Adafruit_NeoPixel pixels = Adafruit_NeoPixel(NUM_LED, LED_PIN, NEO_GRB + NEO_KHZ800);

// battery
ESP32AnalogRead adc;
#define ADCpin 0
#define DividerRatio 1.7693877551

// ps button
#define OFF_PIN 5

esp_now_peer_info_t peerInfo;

struct Message {
  LaskaGamepad gamepad_inputs;
  uint8_t battery_v; // voltage * 10
};

Message message;

// power off
float batt_min = 3.0;
float batt_warn = 3.2;

LaskaGamepad laska_gamepad;


// for debugging
void print_inputs(LaskaGamepad *lg) {
  int16_t *lgg = (int16_t *)lg;
  for (int j = 0; j < 5; j++) {
    Serial.print(j);
    Serial.print(" ");
    for (int i = 0; i < 16; i++) {
      Serial.print((*lgg & (1 << i)) >> i);
    }
    lgg++;
    Serial.println();
  }
}

// for debugging
void print_message(Message *m) { print_inputs(&m->gamepad_inputs); }


int16_t handle_deadzones(int16_t value) {
  // deadzone ends 250
  // deadzone center 800
  if (abs(value) < 800) {
    return 0;
  }
  if (value > (1 << 15) - 1 - 250) {
    return (1 << 15) - 1;
  }
  if (value < -(1 << 15) + 250) {
    return -(1 << 15);
  }
  return value;
}

uint16_t convert_to_16_bit(int32_t raw_value) {
  // 65535 / 26490
  return raw_value * 4369 / 1766 - (1 << 15);
}

int16_t read_gamepad_stick_adc(uint8_t n) {
  return handle_deadzones(convert_to_16_bit(ADS.readADC(n)));
}

void read_gamepad() {
  // read sticks
  laska_gamepad.left_stick_y = read_gamepad_stick_adc(0);
  laska_gamepad.left_stick_x = read_gamepad_stick_adc(1);
  laska_gamepad.right_stick_y = read_gamepad_stick_adc(2);
  laska_gamepad.right_stick_x = read_gamepad_stick_adc(3);

  // read buttons
  laska_gamepad.buttons = ~(PCF.read16());

  // read power_off button
  laska_gamepad.off = !digitalRead(OFF_PIN);
}

void setup() {
  Serial.begin(115200);

  // p3 button
  pinMode(OFF_PIN, INPUT);

  // neopixels
  pixels.begin();
  pixels.setBrightness(BRIGHTNESS);


  // i2c
  Wire.begin(8, 10);
  ADS.begin();

  // voltage on gamepad stick is 0-3V3 (3.31) safe margin
  // so the raw value is between 0 and 26400 (26480) in theory
  // there are some deadzones
  adc.attach(ADCpin); // battery
  ADS.setGain(1); // +- 4.096 V
  PCF.begin();

  WiFi.mode(WIFI_STA);
  esp_now_init();
  esp_now_set_pmk((uint8_t *)PMK_KEY_STR);

  // setup peer info
  memcpy(peerInfo.peer_addr, car_mac_address, 6);
  peerInfo.channel = 0;
  peerInfo.encrypt = true;
  memcpy(peerInfo.lmk, LMK_KEY_STR, 16);

  if (esp_now_add_peer(&peerInfo) != ESP_OK) {
    Serial.println("Failed to add peer");
  }
}

void loop() {
  read_gamepad();
  message.gamepad_inputs = laska_gamepad;

  // read battery
  float batt_voltage = adc.readVoltage() * DividerRatio * 10;
  message.battery_v = batt_voltage;

  esp_err_t result = esp_now_send(car_mac_address, (uint8_t *)&message, sizeof(message));
  if (result == ESP_OK) {
    pixels.setPixelColor(1, pixels.Color(0, 255, 0)); // R, G, B
    pixels.show();
    Serial.println("Sent with success");
  } else {
    pixels.setPixelColor(1, pixels.Color(255, 0, 0)); // R, G, B
    pixels.show();
    Serial.println("Error sending the data");
  }
  delay(10);
}

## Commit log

2025-04-25 Add SW example using omni wheels and gamepad.
2025-05-23 Keep one ESP-NOW peer. Add timed power off button.
2025-10-19 new ver
    [ESP_Robo_Board_V2 v35_bom.csv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]
2025-11-24 Update ESP_Robo_Board_V2 v35_bom.csv
    [ESP_Robo_Board_V2 v35_bom.csv]
2025-11-24 Update ESP_Robo_Board_V2 v35_cpl.csv
    [ESP_Robo_Board_V2 v35_cpl.csv]

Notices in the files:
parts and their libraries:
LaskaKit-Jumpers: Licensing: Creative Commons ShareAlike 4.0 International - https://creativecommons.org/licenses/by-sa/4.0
